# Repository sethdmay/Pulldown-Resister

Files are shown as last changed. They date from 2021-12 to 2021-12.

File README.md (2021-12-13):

# Pulldown Resister: An Automatic Face Mask Raiser
_developed by Seth May_

## Executive Summary
Due to the COVID-19 Pandemic, it is in the interest of public health that people wear face masks or coverings inside to
reduce the spread of the virus. 
Sometimes people forget to pull their mask off their chin when they go inside. They might also be physically unable to do
so, either due to a disability or because their hands are filled.
I propose the Pulldown Resister, a device that automatically detects when a person goes inside and pulls up their mask.
This device improves mask adherence in public, while also offering an aid to those whom it may be difficult to manually
raise their mask

## Visual Story

The general visual story can be found [in the images folder](images/visualstory.pdf).

## Components Used

| Component | Function | Link |
|---|---|---|
| Adafruit Feather M4 Express - Featuring ATSAMD51 | Microcontroller/The Brain | https://www.adafruit.com/product/3857 |
| Adafruit AMG8833 IR Thermal Camera Breakout | Temperature Sensor | https://www.adafruit.com/product/3538 |
| Adafruit LTR390 UV Light Sensor | UV Light Sensor | https://www.adafruit.com/product/4831 |
| Maxbotix Ultrasonic Rangefinder - LV-EZ0 | Distance Sensor | https://www.adafruit.com/product/979  |
| Micro Servo - MG90D High Torque Metal Gear | Actuation of Mask | https://www.adafruit.com/product/1143 |
| Adafruit Wii Nunchuck Breakout Adapter | Interface Nunchuck with Device | https://www.adafruit.com/product/4836 |
| Wii Nunchuck | Manual Control | Many sources exist |
| Many 3D Printed Parts (Translucent Blue PLA) | Structure | [See CAD Folder for STEP files](CAD)  |

## Implementation

### Overview

There are 2 main parts of the device: the mask actuator and the sensor housing. 

The mask actuator consists of a non-moving back piece, which attaches to the moving front piece via 2 hinges. Each side has a different hinge, since 1 of them accommodates the servo.
The front piece can be attached to the joints via tape or glue, and the motor can be attached to the join similarly. The joint
with the motor fits into the back piece as more of an interference fit to ease removal of the whole device from the head. 

The sensor housing consists of a main box with a cover. The box has space to hold a breadboard with all the components and sensors, shown below.
There are also cutouts to accomodate a Micro USB cable for the Feather M4 and the Nunchuck plug. At one end of the box there are
holes for string, a chain, or some other necklace-type item to wear the box.

### Hardware

For indoor/outdoor detection I used the LTR390. Based on some experiments, I found that the sensor gave a non-zero reading of UV light in full
sunlight, in shade, and in cloudy weather. Inside, even by windows, there was no UV light detected, with the exception of when the sensor was
near older incandescent light bulbs. Since many lightbulbs are now LED, this is not a pressing issue.

For person detection I used the AMG8833 combined with the LV-EZ0 to detect if there was (a) a warm mass - likely a person - in the field of
view and (b) if there was an object within ~6 feet. If both (a) and (b) were true, the device decides there is a person within 6 feet and
the mask should be raised. One shortcoming of this methodology is that heaters like radiators or heat lamps also fulfill this criteria,
although radiators are unlikely to be outside.

I used a Wii Nunchuck and the Adafruit breakout board for testing of the mechanism, and for some demonstration purposes. This method of device
actuation could have uses for people who can't raise their arms or have other limited mobility.

For actuation of the mask, I used the Micro Servo, which was attached to the main moving piece of the mechanism. It rotated on the joint between
the moving and stationary piece, which rotated the whole mechnaism, and had sufficient torque to do so.

### Software

The code is written in CircuitPython, specifically version 7.0.0 for the Adafruit Feather M4 Express, but the code could likely work on any
dev board that supports CircuitPython, has sufficient flash memory for the libraries, supports I2C, and has 1 pin of PWM. The most up to date
[libraries](https://circuitpython.org/libraries) and firmware can be found at
the [CircuitPython website](https://circuitpython.org/board/feather_m4_express/).

The code is all in [code.py](code.py).

### CAD

The STEP files in the [CAD](CAD/) folder are enough to 3D print all of the mechanisms. 1 of each STEP file should be printed for a full assembly.
Additionally, the .f3d and.f3z files can be used in Autodesk Fusion 360 and probably imported into other CAD software if you want to edit
anything.

## Pictures

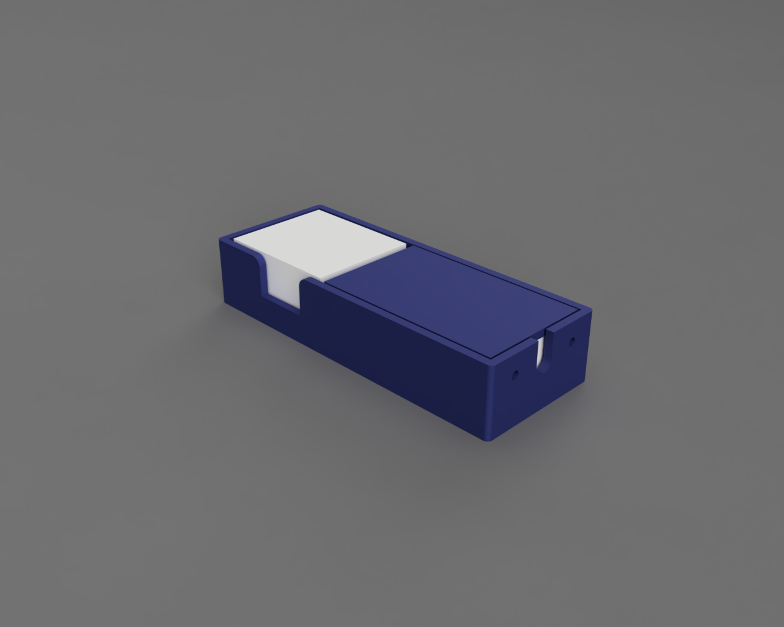
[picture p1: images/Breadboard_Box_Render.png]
CAD of the Breadboard Box

_CAD of the Breadboard and Sensor Housing_

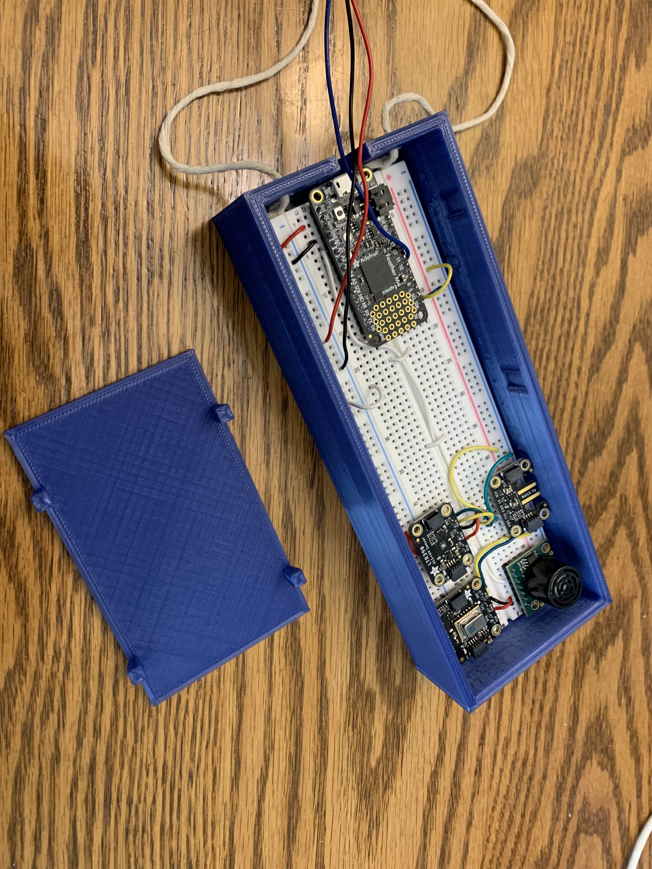
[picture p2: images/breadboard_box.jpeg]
actual breadboard box

_Actual Breadboard and Sensor Housing_

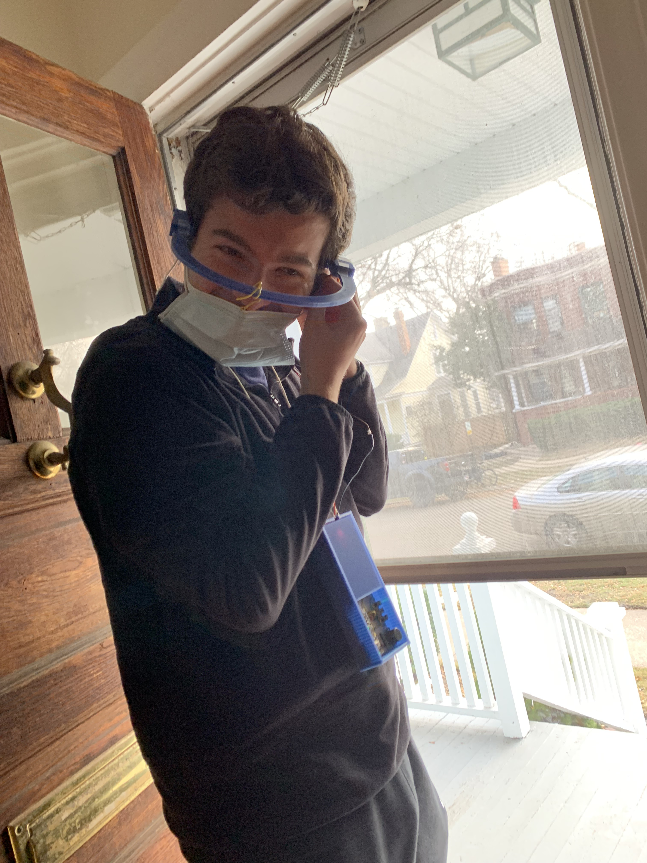
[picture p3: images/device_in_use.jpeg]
person wearing device

_Device being put on by user_

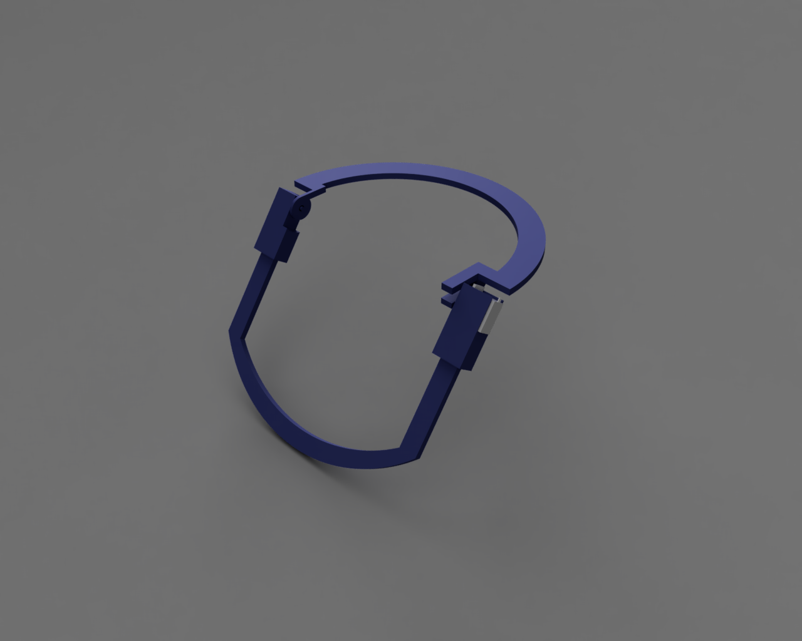
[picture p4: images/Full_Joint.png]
CAD of the mask mechanism

_CAD of the mask actuator, the moving piece is on the left while the stationary piece is on the right_

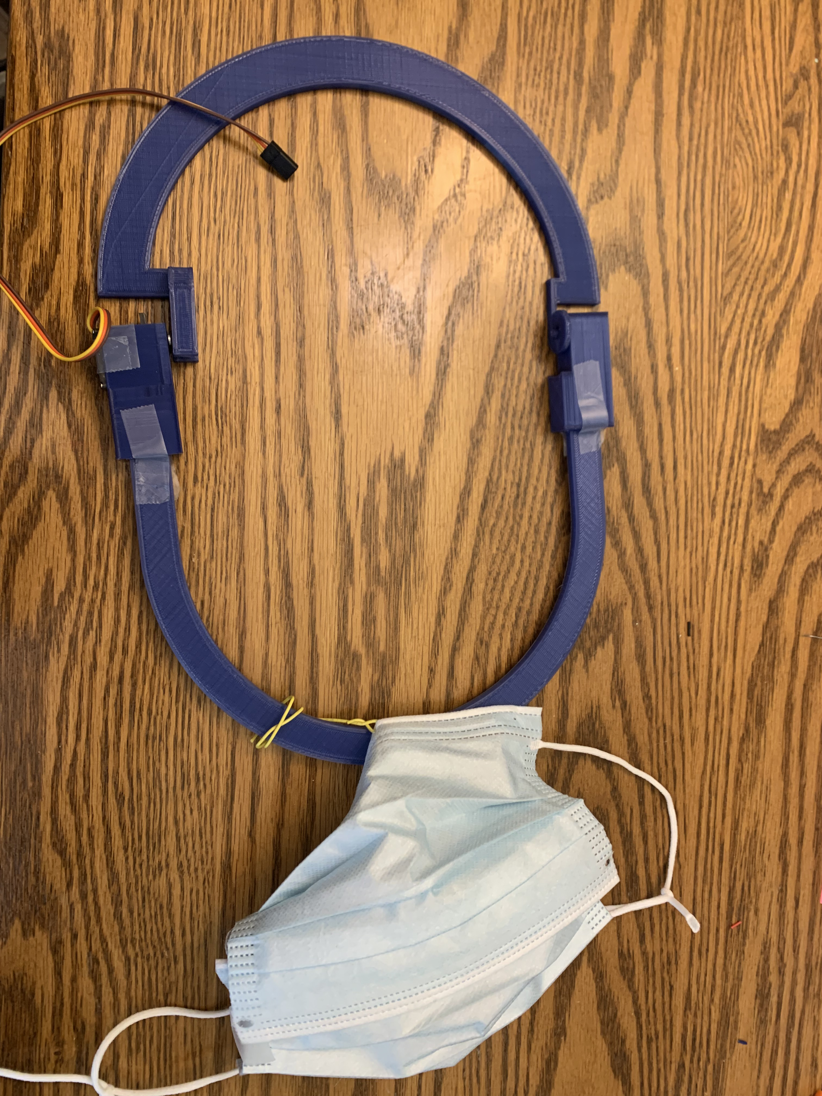
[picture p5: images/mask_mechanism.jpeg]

_The real mask actuator, showing the motor at the bottom, and where the mask would go on the right._
_Here, the stationary piece is on the left and the moving piece is on the right_
## Post Mortem

1. The most complicated subsystem to get working was the actual mechanism that raised and lowered the mask. I limited myself to primarily
   raising the mask, since you wouldn't want a scenario where a sensor malfunctions and the mask lowers itself when it shouldn't. The mechanism
   can do up and down, but it's better tuned to raising the mask. Even so, the mask is very loose across the face, and I had to use a modified 
   mask of 2 masks put together so it doesn't get stuck. An optimal system would likely need to move the nose brace in a non-circular path, in order to clear both the nose and chin.
2. Ultrasonic sensors can a bit finicky, especially when working with people and a sensor mounted on a mobile platform (another person). In
   hindsight, a camera with computer vision may work better to identify people (although some CV algorithms have bias issues).
3. 3D Printing is really great and useful for being able to quickly make good prototype and even production-level parts, but it can be slow. For
   some of my prototyping, making a mockup out of cardboard or foamboard may have helped figure out some of the actuation issues. 3D printing is
   still really useful since you can mockup the design in CAD and perfectly reproduce that with a 3D printer rather than by hand.

## Further Notes

Project for CompE 395 @ Northwestern w/ Josiah Hester

Code is written in CircuitPython for an Adafruit Feather M4 Express  
Specific Feather M4 Express and libraries included are for CircuitPython 7.0.0  
Most up to date [libraries](https://circuitpython.org/libraries) and firmware can be found at the [CircuitPython website](https://circuitpython.org/board/feather_m4_express/)

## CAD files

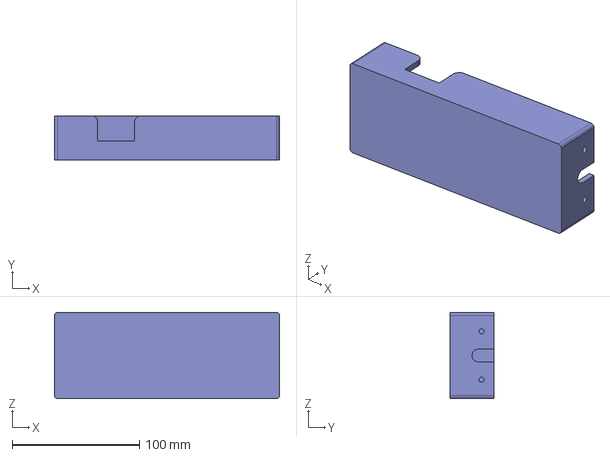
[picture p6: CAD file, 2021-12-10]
CAD/Main Case Body.step
177.0 x 35.0 x 68.0 mm

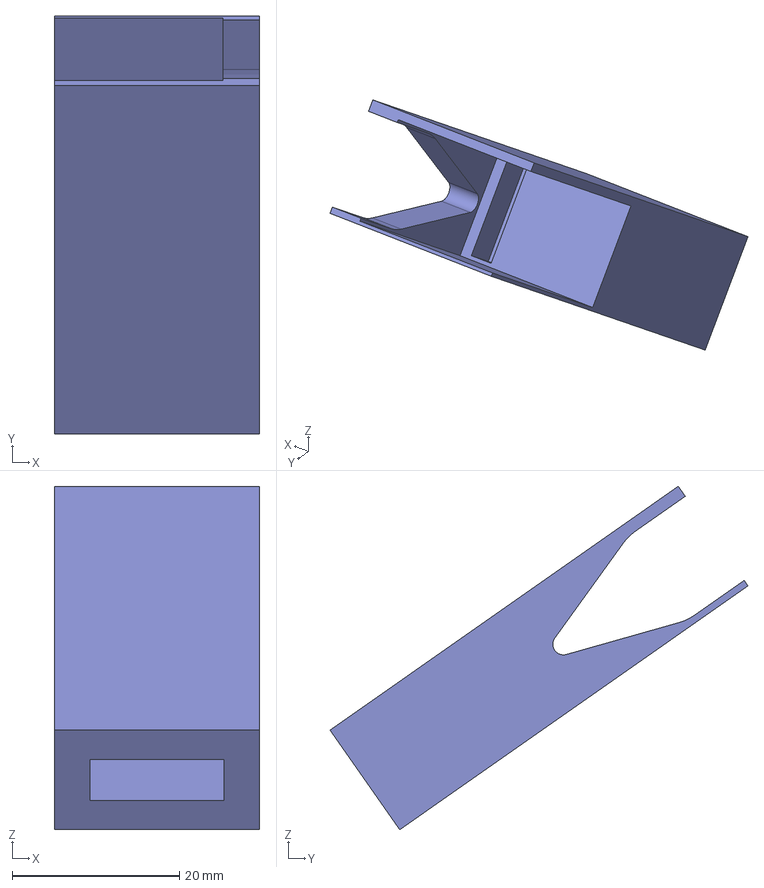
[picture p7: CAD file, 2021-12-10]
CAD/Motor Joint.step
24.5 x 49.9 x 41.0 mm

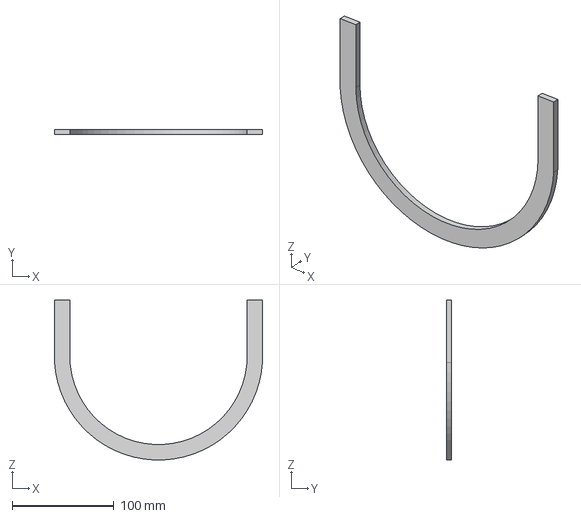
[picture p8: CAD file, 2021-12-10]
CAD/Nose Bridge.step
204.0 x 5.00 x 156.8 mm

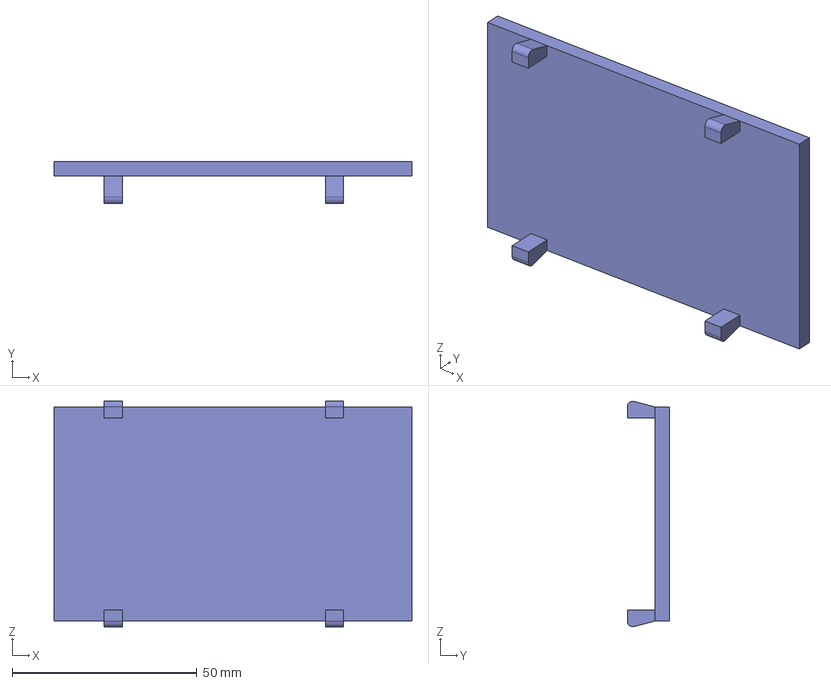
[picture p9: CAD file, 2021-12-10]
CAD/Top Cover.step
97.0 x 11.5 x 61.1 mm

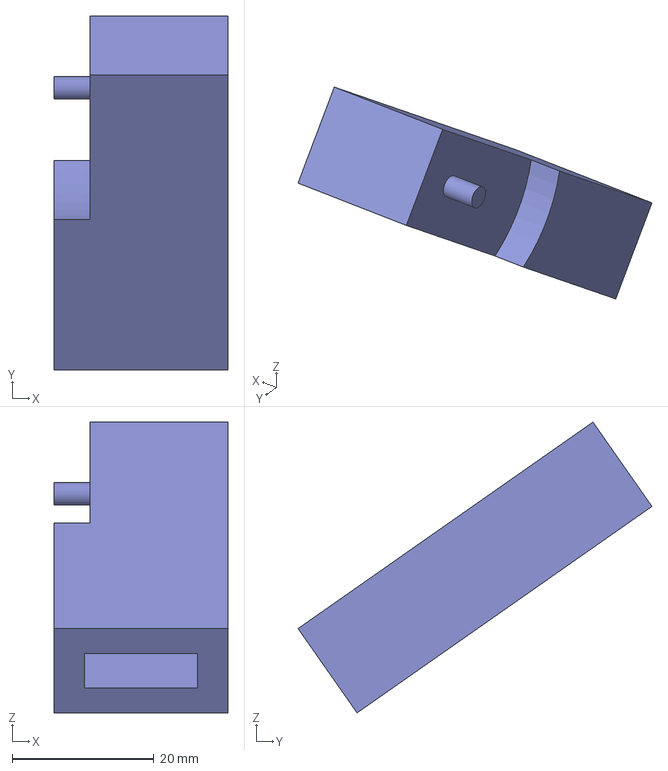
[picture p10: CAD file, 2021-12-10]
CAD/Non-Motor Joint.step
24.5 x 49.9 x 41.0 mm

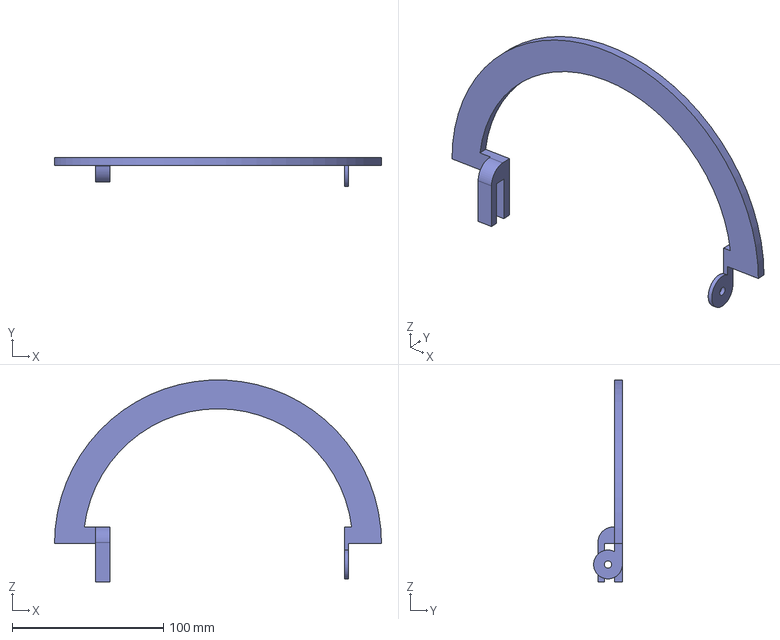
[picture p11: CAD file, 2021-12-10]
CAD/Rear Fixed Part.step
215.9 x 19.0 x 133.2 mm

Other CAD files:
CAD/Breadboard Box Fusion.f3d
CAD/Mask Actuation Assembly.f3z
CAD/Nose Bridge.f3d

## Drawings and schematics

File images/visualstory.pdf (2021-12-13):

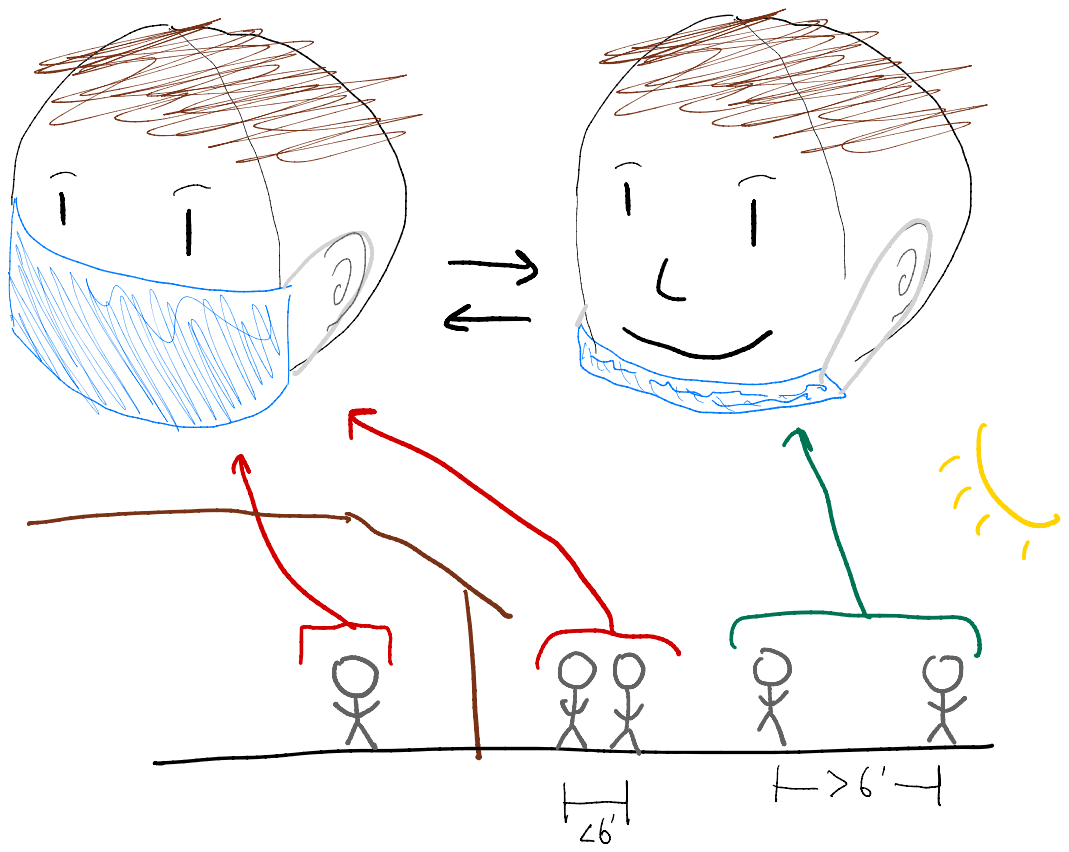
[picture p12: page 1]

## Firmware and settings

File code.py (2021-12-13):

"""CircuitPython Essentials: PWM with Fixed Frequency example."""
import time
import math
import board
import pwmio
import simpleio
import analogio
import adafruit_nunchuk
import adafruit_amg88xx
import adafruit_ltr390
import neopixel

UPPER = 0.095      # lowers the mask
LOWER = 0.05       # raises the mask (yes I know it's confusing)
UV_THRES = 0.1     # accounts for "noise" inside
DIST_THRES = 7600  # approx 6 ft


amg = adafruit_amg88xx.AMG88XX(board.I2C())
ltr = adafruit_ltr390.LTR390(board.I2C())


mtr = pwmio.PWMOut(board.D10, frequency=50, duty_cycle=3276)
npix = neopixel.NeoPixel(board.NEOPIXEL, 1, brightness=0.5)
# nc = adafruit_nunchuk.Nunchuk(board.I2C())

ultra = analogio.AnalogIn(board.A0)

def map_duty(frac):
    return int(simpleio.map_range(frac, 0, 1, 0, 65535))
# 2000 to 7700 -> 0.03 to 0.11

def top_5_avg(temps):
    temps = [item for sublist in temps for item in sublist]
    sorted_temps = sorted(temps, reverse=True)
    return sum(sorted_temps[0:5])/5

def convert_temp(temp):
    char = ""
    if temp <= 23:
        char = "."
    elif temp <= 24:
        char = "o"
    elif temp <= 26:
        char = "O"
    elif temp >= 27:
        char = "#"
    
    return char

def ranger(dist):
    out = "["
    for i in range(int(30*dist/14000)):
        out += "#"

    out += "]"

    return out

# motor
inside = False
duty_cycle = UPPER

# UV light
cycles = 0

# temp
running_average = [0,0,0,0,0]
warm = False

# distance
state_buffer = 0
detect = False


while True:
    ### NUNCHUCK
    # x, y = nc.joystick

    # incr = simpleio.map_range(y, 255, 1, -0.002, 0.002)
    # duty_cycle += incr

    # if duty_cycle < LOWER:
    #     duty_cycle = LOWER
    # elif duty_cycle > UPPER:
    #     duty_cycle = UPPER

    # if nc.buttons.C:
    #     duty_cycle = UPPER
    # elif nc.buttons.Z:
    #     duty_cycle = LOWER

    ### DISTANCE SENSOR
    if detect:
        # we think theres a person
        if ultra.value > DIST_THRES:
            state_buffer += 1
            if state_buffer >= 8:
                detect = False
                state_buffer = 0
                # kit.servo[0].angle = 90
        else:
            state_buffer = max(0,state_buffer-1)
    else:
        # currently no one nearby
        if ultra.value < DIST_THRES:
            state_buffer += 1
            if state_buffer >= 8:
                detect = True
                state_buffer = 0
                # kit.servo[0].angle = 0
        else:
            state_buffer = max(0,state_buffer-1)

    ### UV SENSOR

    uv = ltr.uvs
    if not inside:
        if uv <= UV_THRES:
            cycles += 1
            if cycles > 8:
                inside = True
                cycles = 0
        else:
            cycles = 0
    else:
        if uv >= UV_THRES:
            cycles += 1
            if cycles > 8:
                inside = False
                cycles = 0
        else:
            cycles = 0

    print(uv)

    ### IR TEMP SENSOR
    running_average = running_average[1:5]
    running_average.append(top_5_avg(amg.pixels))
    print(running_average)

    if sum(running_average)/5 < 21.5:
        # nothing warm there
        warm = False
    else:
        warm = True

    if inside:
        # Raise mask on inside
        duty_cycle = LOWER
    elif warm and detect:
        # theres something nearby that's warm, raise the mask
        duty_cycle = LOWER
    else:
        # we're outside, there's nothing warm AND near, lower the mask
        # TODO: gate this so normal operation doesn't lower mask
        duty_cycle = UPPER

    # some nice lighing stuff that shines green when mask should be down, red when up
    if duty_cycle == LOWER:
        npix.fill(0xFF0000)
    else:
        npix.fill(0x00FF00)

    ### MOTOR

    mtr.duty_cycle = map_duty(duty_cycle)
    print(mtr.duty_cycle, " --- dc: ", duty_cycle)



    print("**" if detect else "  ", ultra.value, ranger(ultra.value))
    time.sleep(0.05) # 20 Hz is the max rate of the distance sensor
